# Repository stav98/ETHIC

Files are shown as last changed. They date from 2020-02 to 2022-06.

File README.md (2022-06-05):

# ETHIC
Αποθετήριο με οδηγίες κατασκευής, πηγαίο κώδικα και σχέδια για το έργο " Έξυπνο Θερμοκήπιο Υδροπονικής Καλλιέργειας "<br>
**Ομάδα:** ΚΟΤΣΑΝΙΑ Α.Ε. <br/>
**Σχολείο:** 1ο ΕΠΑ.Λ. Πρέβεζας - Ε.Κ. Πρέβεζας (2019-20, 2020-21)<br/>
**Τίτλος έργου:** Έξυπνο Θερμοκήπιο Υδροπονικής Καλλιέργειας (Ε.Θ.Υ.Κ.)<br/> 

<b>Τελευταία ενημέρωση 5-6-2022</b>

Περιγραφή έργου - Στόχοι
========================
Η ομάδα μας στα πλαίσια του <a href="https://openedtech.ellak.gr/robotics2021/exipno-thermokipio-idroponikis-kalliergias-1o-epa-l-prevezas/">Διαγωνισμού Ανοιχτών Τεχνολογιών στην Εκπαίδευση</a> ο οποίος διοργανώνεται από τον <a href="https://eellak.ellak.gr/">ΕΕΛΛΑΚ</a>, κατασκεύασε <b>μακέτα</b> σύγχρονου θερμοκηπίου υδροπονικής καλλιέργειας το οποίο ελέγχεται εξ' ολοκλήρου από Η/Υ. Το σύστημα εκτός από την δυνατότητα τηλεχειρισμού των λειτουργιών, έχει την δυνατότητα λήψης αποφάσεων ώστε να τηρούνται οι κατάλληλες συνθήκες για την σωστή ανάπτυξη των φυτών. Επιπλέον θα υπάρχει η δυνατότητα αποθήκευσης και γραφικής προβολής όλων των δεδομένων ώστε ο παραγωγός να μπορεί να συσχετίζει την εξέλιξη της παραγωγής σε συνάρτηση με τις συνθήκες του θερμοκηπίου. Έτσι μπορεί να δημιουργήσει μια βάση δεδομένων από την οποία θα αντλεί χρήσιμες πληροφορίες για το κάθε είδος ώστε να μεγιστοποιηθεί η παραγωγή.

Είμαστε μαθητές του τομέα πληροφορικής του 1ου ΕΠΑ.Λ. Πρέβεζας. Η υλοποίηση του έργου έγινε στα εργαστήρια του Ε.Κ. Πρέβεζας μετά την λήξη του διδακτικού ωραρίου.

<table align="center">
 <tr>
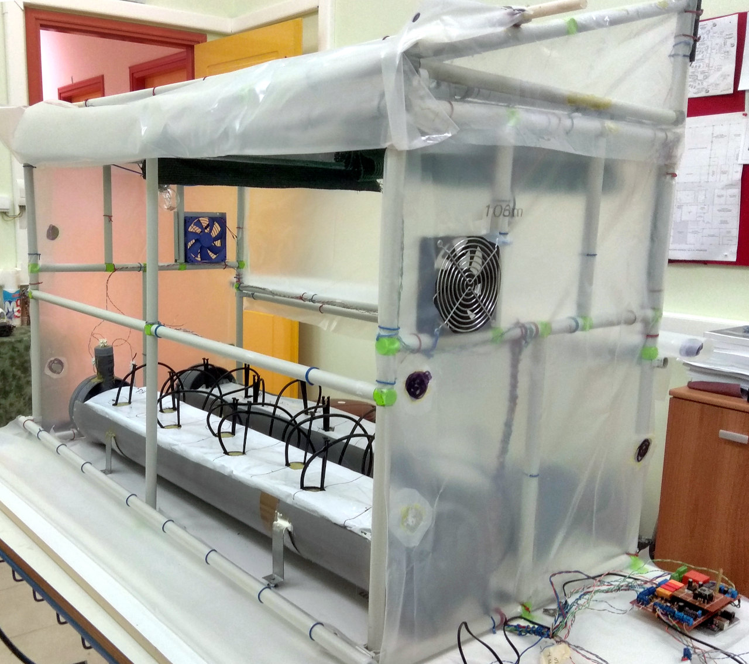
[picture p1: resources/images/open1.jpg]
  <td></td>
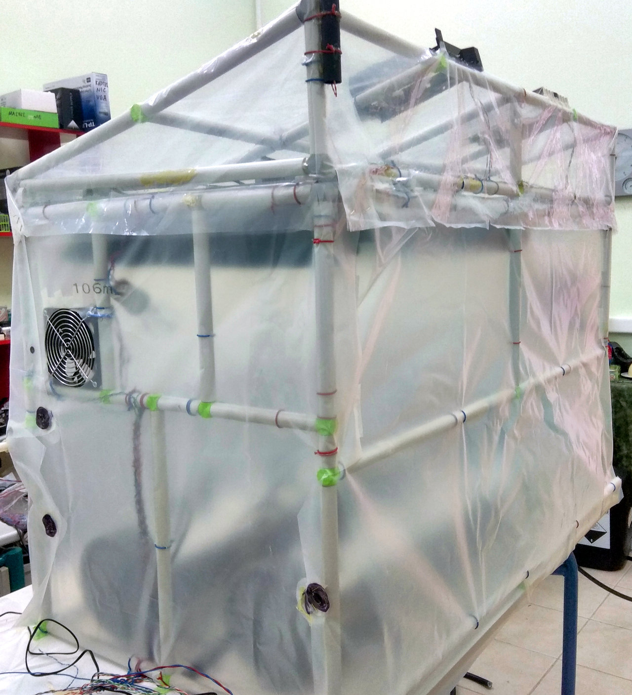
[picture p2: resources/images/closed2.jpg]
  <td></td>
  </tr>
 </table>

Περιεχόμενα
===========

<a href="/md_docs/eisag1.md">Εισαγωγή. Τι είναι η υδροπονία;</a><br>
<a href="/md_docs/eisag2.md">Αρχικός σχεδιασμός του έργου - Στόχοι - Απαιτήσεις και προδιαγραφές.</a><br>
<a href="/md_docs/en6.md">Επίσκεψη σε θερμοκήπιο υδροπονικής καλλιέργειας.</a><br>
<a href="/md_docs/en1.md">Σχεδιασμός μακέτας.</a><br>
<a href="/md_docs/en3.md">Κατασκευή μακέτας.</a><br>
<a href="/md_docs/electrolog.md">Η ηλεκτρολογική εγκατάσταση.</a><br>
Οι συσκευές εξόδου (ενεργοποιητές):<br>
&nbsp;&nbsp;&nbsp;&nbsp;&nbsp;<a href="/md_docs/potisma.md">Το σύστημα ποτίσματος.</a><br>
&nbsp;&nbsp;&nbsp;&nbsp;&nbsp;<a href="/md_docs/skiasi.md">Το σύστημα σκίασης.</a><br>
&nbsp;&nbsp;&nbsp;&nbsp;&nbsp;<a href="/md_docs/eksaerismos.md">Το σύστημα εξαερισμού.</a><br>
&nbsp;&nbsp;&nbsp;&nbsp;&nbsp;<a href="/md_docs/window.md">Τα παράθυρα οροφής.</a><br>
&nbsp;&nbsp;&nbsp;&nbsp;&nbsp;<a href="/md_docs/heating.md">Το σύστημα θέρμανσης.</a><br>
<a href="/md_docs/sensors.md">Οι συσκευές εισόδου (αισθητήρες).</a><br>
<a href="/md_docs/en2.md">Τα ψηφιακά υποσυστήματα ελέγχου και επικοινωνίας.</a><br>
&nbsp;&nbsp;&nbsp;&nbsp;&nbsp;<a href="/md_docs/thermo_node.md">Ο κόμβος ελέγχου των λειτουργιών του θερμοκηπίου.</a><br>
&nbsp;&nbsp;&nbsp;&nbsp;&nbsp;<a href="/md_docs/LoRa_Gateway.md">Η πύλη LoRa Wan Lite.</a><br>
<a href="/md_docs/en4.md">Το πρωτόκολλο LoRa WAN Lite.</a><br>
<a href="https://github.com/stav98/ETHIC/tree/master/NodeRed">Node Red - Η λογική των αυτοματισμών και το γραφικό περιβάλλον.</a><br>

Συμμετέχοντες μαθητές
=====================
<ul>
 <li>Θεοφάνους Ευαγγελία</li>
 <li>Λίτσι Άλντο</li>
 <li>Μιχαηλίδης Γιώργος</li>
 <li>Νέσσερης Θοδωρής</li>
</ul>

Υπεύθυνος καθηγητής: Σταύρος Φώτογλου ΠΕ86 πληροφορικής

Χρονοδιάγραμμα - Στάδια υλοποίησης του έργου
===========================
01/12/19 - 20/12/19 : <a href="md_docs/en1.md">Αρχικός σχεδιασμός ιδέας</a><br/>
08/01/20 - 18/01/20 : <a href="md_docs/en2.md">Σχεδιασμός Hardware</a><br/>
19/01/20 - 29/01/20 : <a href="md_docs/en3.md">Σχεδιασμός 3D εξαρτημάτων και εκτύπωση στον 3D printer</a><br/>
23/01/20 - 30/01/20 : <a href="md_docs/en4.md">Μελέτη πρωτοκόλλου LoRa WAN και κατασκευή του δικού μας απλοποιημένου LoRa WAN Lite</a><br>
01/02/20 - 18/02/20 : Παραγγελία υλικών και ηλεκτρονικών εξαρτημάτων - Έναρξη κατασκευής σκελετού<br>
19/02/20 - 19/02/20 : <a href="md_docs/en6.md">Επίσκεψη σε θερμοκήπιο υδροπονικής καλλιέργειας</a><br/>
20/02/20 - 20/03/20 : Κατασκευή μηχανικών μερών, συστήματος άρδευσης<br/>
............ Διακοπή εργασιών λόγω της πανδημίας ...................<br>
Απρίλιος '21 : Κατασκευή υδραυλικών - αρδευτικών συστημάτων.<br> 
&nbsp;&nbsp;&nbsp;&nbsp;&nbsp;&nbsp;&nbsp;&nbsp;&nbsp;-//-&nbsp;&nbsp;&nbsp;&nbsp;&nbsp;&nbsp;&nbsp;&nbsp;: Δοκιμές άρδευσης.<br>
&nbsp;&nbsp;&nbsp;&nbsp;&nbsp;&nbsp;&nbsp;&nbsp;&nbsp;-//-&nbsp;&nbsp;&nbsp;&nbsp;&nbsp;&nbsp;&nbsp;&nbsp;: Κατασκευή συστήματος σκίασης - Δοκιμές.<br>
Μάϊος '21    : Πέρασμα καλωδίωσης - ηλεκτρολογική εγκατάσταση.<br>
&nbsp;&nbsp;&nbsp;&nbsp;&nbsp;&nbsp;&nbsp;&nbsp;&nbsp;-//-&nbsp;&nbsp;&nbsp;&nbsp;&nbsp;&nbsp;&nbsp;&nbsp;: Τοποθέτηση συστημάτων ποτίσματος - δοκιμές.<br>
&nbsp;&nbsp;&nbsp;&nbsp;&nbsp;&nbsp;&nbsp;&nbsp;&nbsp;-//-&nbsp;&nbsp;&nbsp;&nbsp;&nbsp;&nbsp;&nbsp;&nbsp;: Τοποθέτηση νάυλον.<br>
Ιούνιος '21  : Διόρθωση αρχικών σχεδίων.<br>
&nbsp;&nbsp;&nbsp;&nbsp;&nbsp;&nbsp;&nbsp;&nbsp;&nbsp;-//-&nbsp;&nbsp;&nbsp;&nbsp;&nbsp;&nbsp;&nbsp;&nbsp;&nbsp;: <a href="md_docs/en15.md">Κατασκευή πρωτότυπου ηλεκτρονικού κυκλώματος σε perfboard.</a><br>
&nbsp;&nbsp;&nbsp;&nbsp;&nbsp;&nbsp;&nbsp;&nbsp;&nbsp;-//-&nbsp;&nbsp;&nbsp;&nbsp;&nbsp;&nbsp;&nbsp;&nbsp;&nbsp;: Δοκιμές του πρωτοκόλλου LoRa WAN Lite. <br>
Σεπτέμβριος '21  : Συγγραφή τεκμηρίωσης - σύνδεση υποσυστημάτων - δοκιμές.<br>
<br>
Το έργο θα βελτιώνεται και αναβαθμίζεται συνεχώς από μαθητές επόμενων τάξεων. <b>Τελευταία ενημέρωση: Μαϊος 2022</b>
<br>
<table align="center">
 <tr>
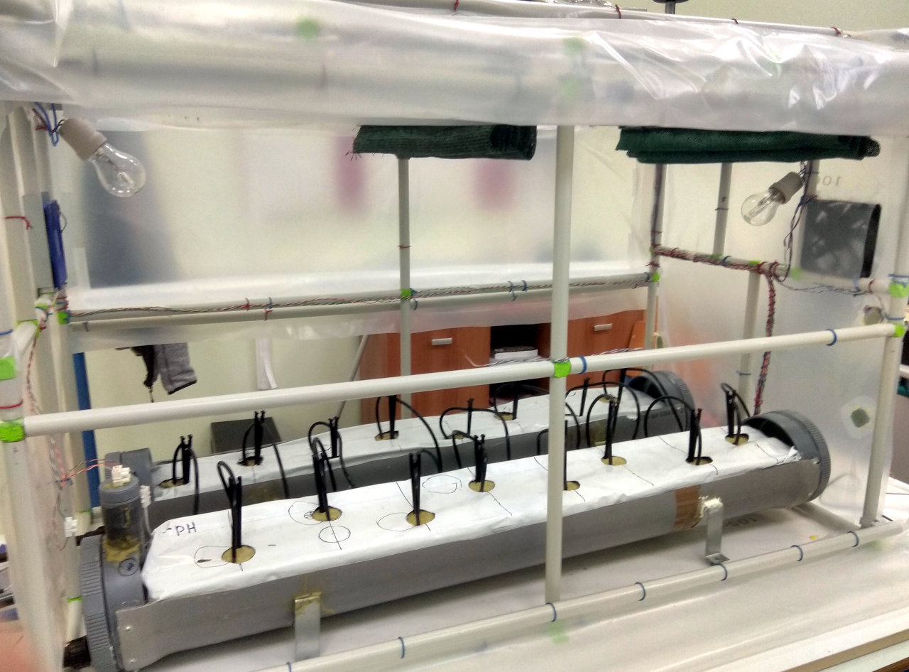
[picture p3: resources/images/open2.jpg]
  <td></td>
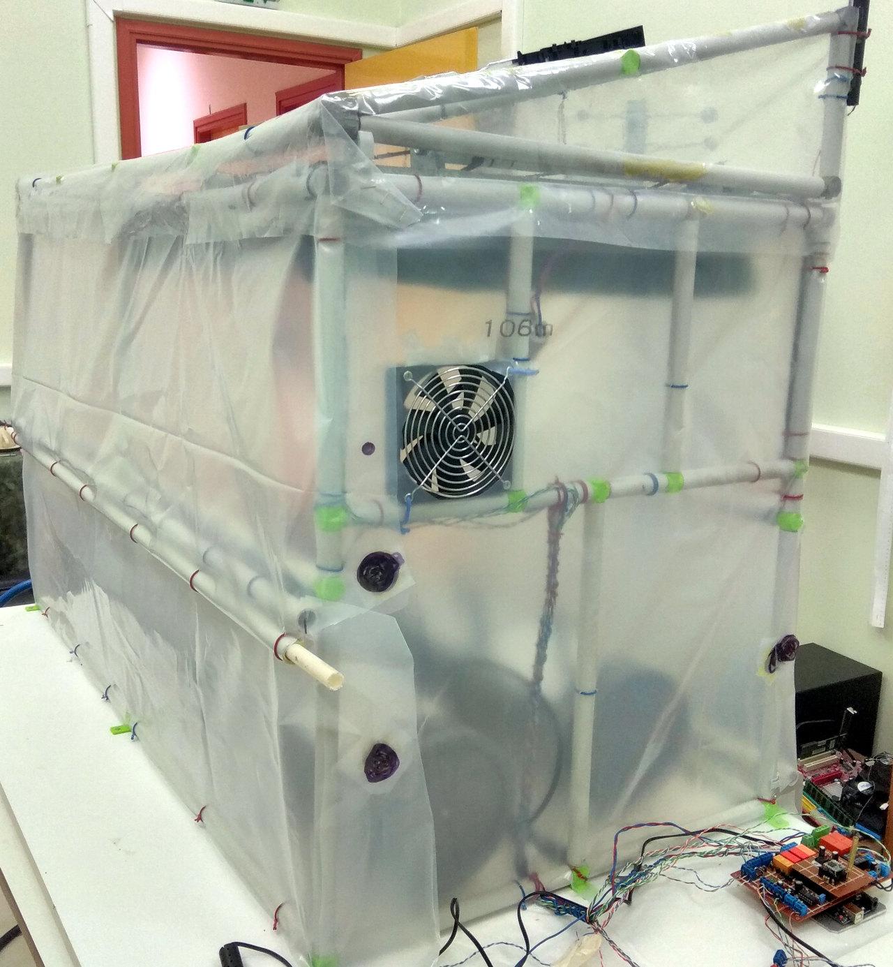
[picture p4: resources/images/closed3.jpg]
  <td></td>
 </tr>
 <tr>
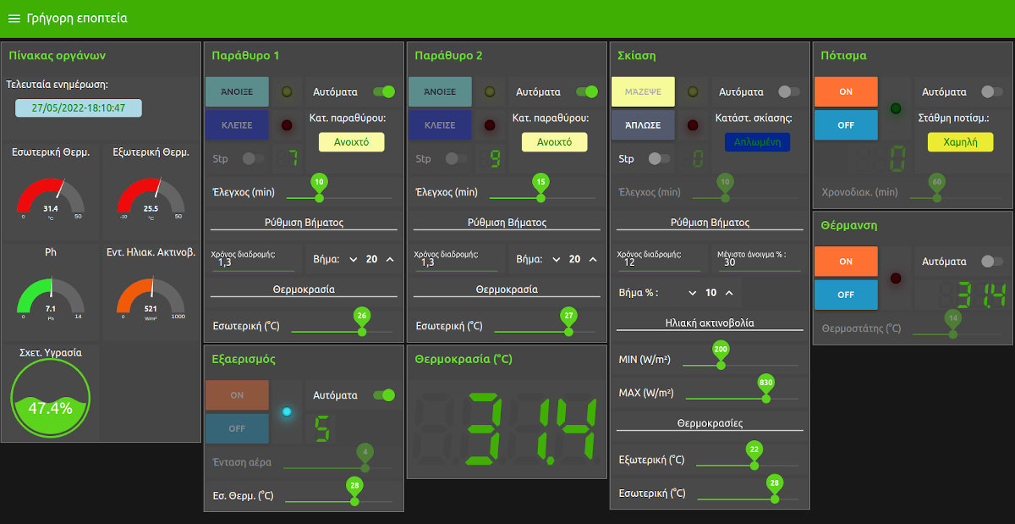
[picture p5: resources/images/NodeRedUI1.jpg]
  <td></td>
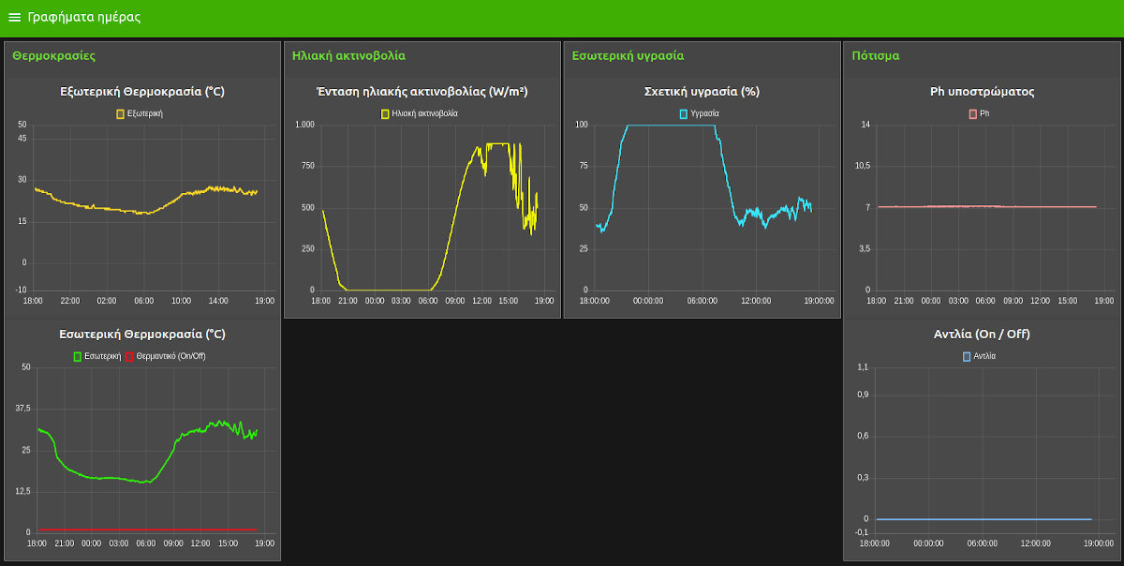
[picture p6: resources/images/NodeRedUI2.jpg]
  <td></td>
 </tr>
 </table>

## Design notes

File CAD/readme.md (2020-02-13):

Στον κατάλογο αυτό υπάρχουν τα σχέδια της κατασκευής καθώς και των εξαρτημάτων τα οποία εκτυπώνονται στον 3D printer.

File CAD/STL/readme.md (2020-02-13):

Εδώ υπάρχουν τα αρχεία των εξαρτημάτων και του μοντέλου σε μορφή .stl, για εκτύπωση στον 3D printer.

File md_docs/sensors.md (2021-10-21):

<a href="../README.md"><= Επιστροφή</a><br>

<p>Παρακάτω φαίνονται οι αισθητήρες του θερμοκηπίου. Για την εξωτερική θερμοκρασία χρησιμοποιήσαμε ένα θερμόμετρο OneWire με ακρίβεια 0,5°C. Για την εσωτερική θερμοκρασία και υγρασία βάλαμε το DHT22. Για την ένταση της ηλιακής ακτινοβολίας Irradiation βάλαμε ένα φτηνό φωτοβολταϊκό από φώτα κήπου. Αυτό σε φορτίο 100Ω παράγει τάση 2V περίπου. Για την πλήρωση της στάθμης ποτίσματος βάλαμε δύο μεταλλικά probe τα οποία μόλις έρθουν και τα δύο σε επαφή με νερό ενημερώνουν τον μικροελεγκτή. Τέλος για μετρητή pH βάλαμε ένα probe από ένα φτηνό όργανο γλάστρας αξίας περίπου 10€. Αυτό έχει μικρή ακρίβεια και μετράει τιμές από 2 (όξινο) έως 12 (αλκαλικό ή βασικό), αλλά για τον σκοπό του έργου μας είναι αρκετό. Το probe του Ph καρφώνεται οριζόντια στο υπόστρωμα του πετροβάμβακα ώστε να μετράει συνέχεια το Ph που υπάρχει στις ρίζες του φυτού. Κάθε καλλιέργεια χρειάζεται τροφή με διαφορετικό Ph ώστε να έχουμε την μέγιστη απόδοση.</p>
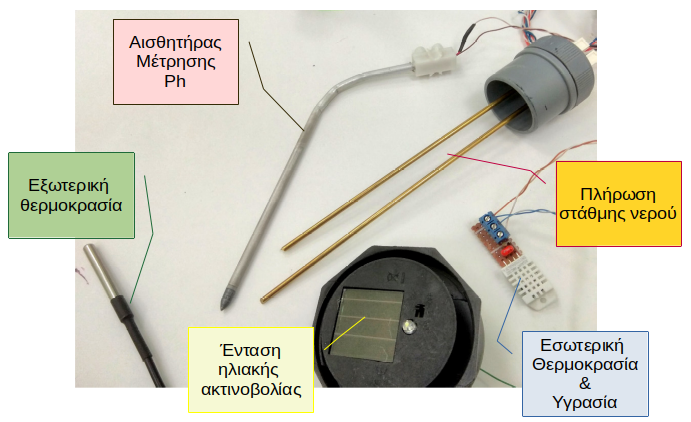
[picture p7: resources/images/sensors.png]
  
  <p>Στην επόμενη εικόνα φαίνονται οι αισθητήρες πλήρωσης και Ph και ο τρόπος που τοποθετούνται. </p>
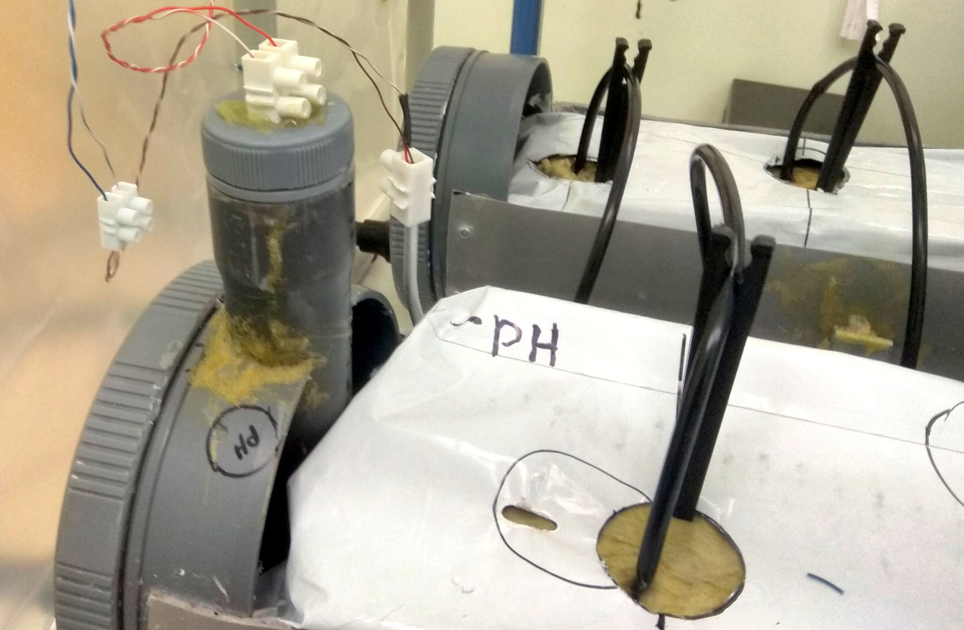
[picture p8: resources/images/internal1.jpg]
  

  <a href="../README.md"><= Επιστροφή</a><br>

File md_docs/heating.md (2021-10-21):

<a href="../README.md"><= Επιστροφή</a><br>

<p>Για θέρμανση χρησιμοποιήσαμε δύο λάμπες πυρακτώσεως των 100W η κάθε μία. Προσοχή οι λάμπες λειτουργούν με 220V. Όταν η εξωτερική θερμοκρασία είναι κάτω από 5°C και η εσωτερική έχει κατέβει κάτω από την ελάχιστη θερμοκρασία ανοχής της καλλιέργειας τότε αυτόματα το Arduino δίνει εντολή και ανάβει τις λάμπες. Φυσικά τα παράθυρα της οροφής είναι κλειστά. Επιπλέον αν δεν υπάρχει ηλιοφάνεια, το σύστημα απλώνει τις κουρτίνες ώστε να μειωθεί ο όγκος του χώρου και να μη χάνουμε θερμότητα από την οροφή.</p>
  

  <a href="../README.md"><= Επιστροφή</a><br>

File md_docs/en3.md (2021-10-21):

<a href="../README.md"><= Επιστροφή</a><br>

<p>Αρχικά σχεδιάσαμε στο λογισμικό ανοιχτού κώδικα FreeCad την μακέτα και εκτυπώσαμε τον σκελετό σε κλίμακα 1:10, ώστε να έχουμε μια εικόνα πριν την έναρξη της κατασκευής. Όλα τα αρχεία για την κατασκευή των εξαρτημάτων <a href="../CAD">βρίσκονται εδώ</a>.</p>
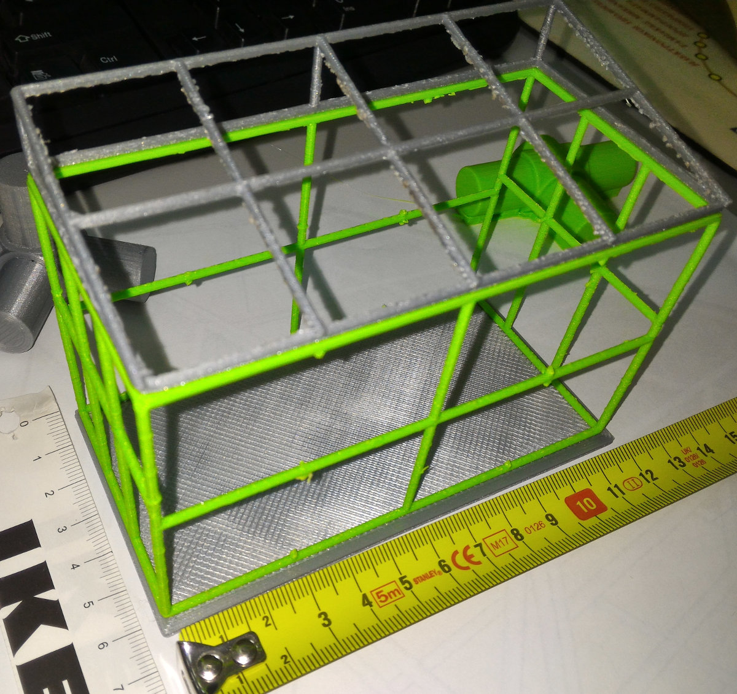
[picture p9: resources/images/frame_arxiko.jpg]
  
<p>Μετά σχεδιάσαμε τα εξαρτήματα των συνδέσμων στο FreeCad και τα εκτυπώσαμε στον εκτυπωτή 3D του σχολείου μας.</p>
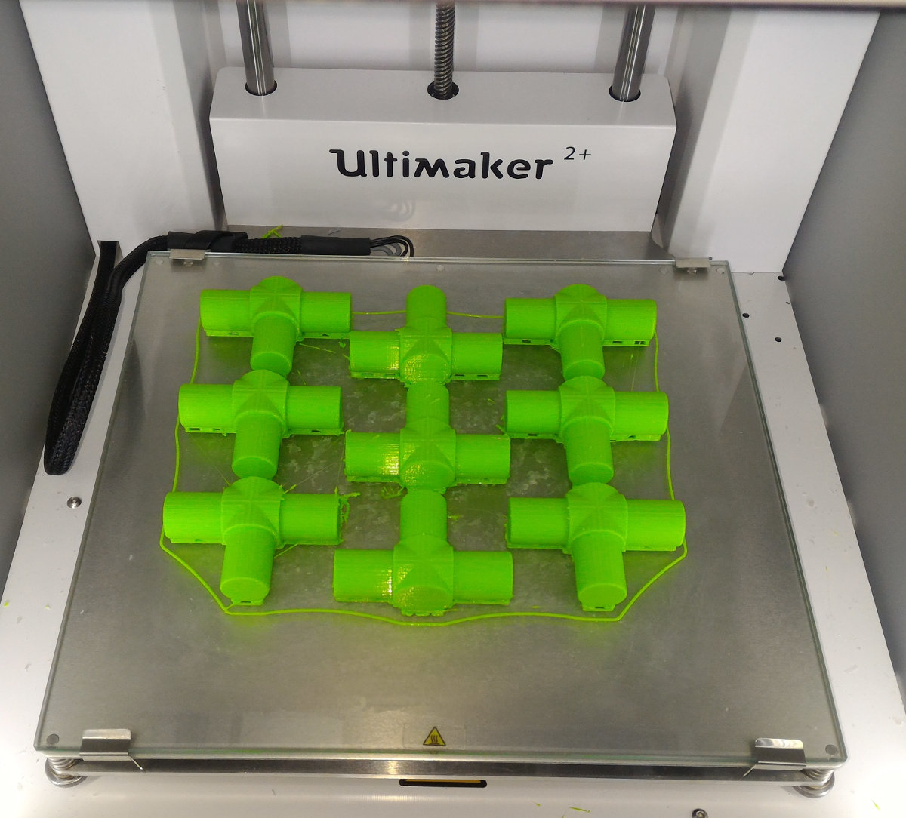
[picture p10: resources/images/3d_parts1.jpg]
  
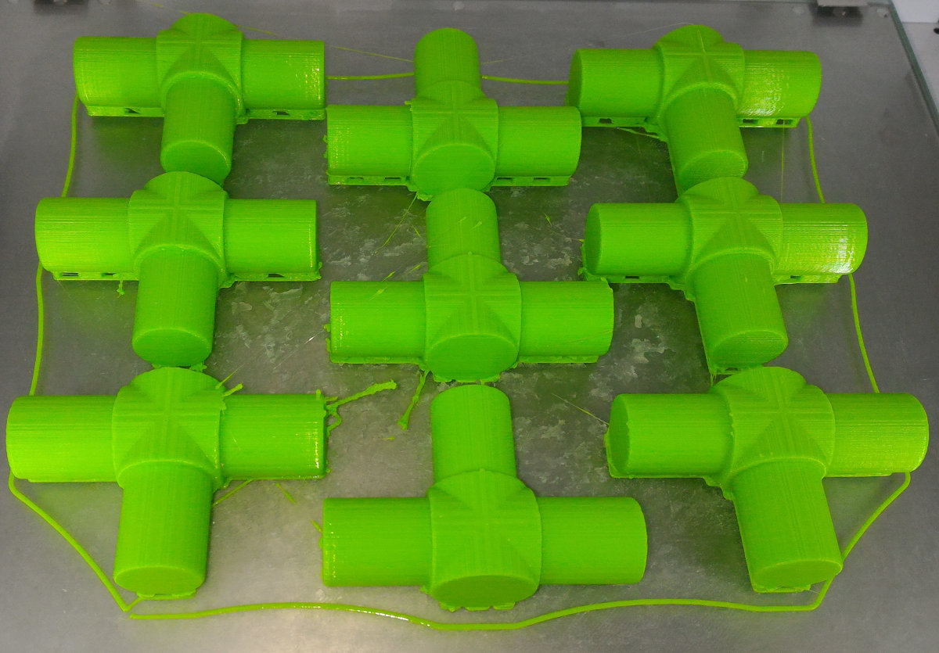
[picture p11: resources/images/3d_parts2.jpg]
  
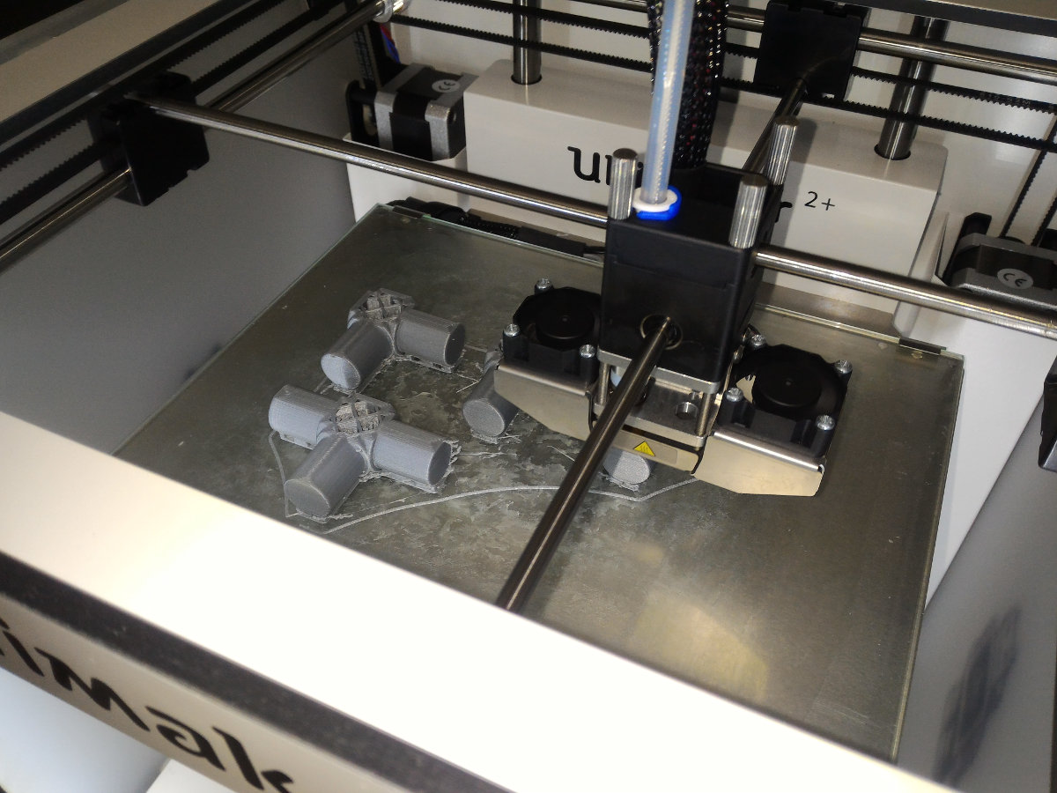
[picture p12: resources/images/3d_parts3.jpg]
  
<p>Ακολουθεί video:</p>
  <p align="center">

</p>
<p>Και μετά συναρμολογήσαμε τον σκελετό της μακέτας. Χρησιμοποιώντας εργαλεία χειρός όπως λίμες, πριόνι και γυαλόχαρτο, εξομαλύναμε τα εξαρτήματα και μετά ενώσαμε τους σωλήνες PVC βάσει του αρχικού σχεδίου.<p>
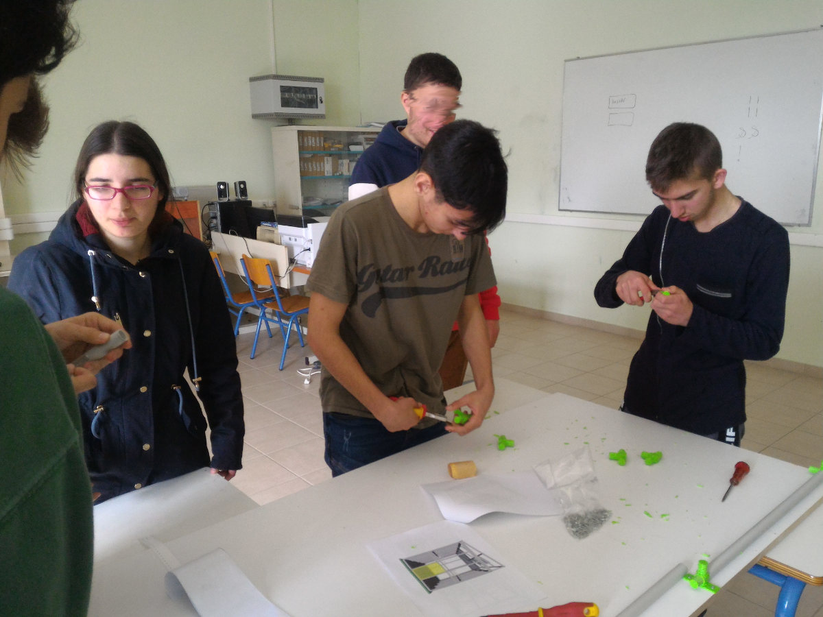
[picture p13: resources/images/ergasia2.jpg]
  
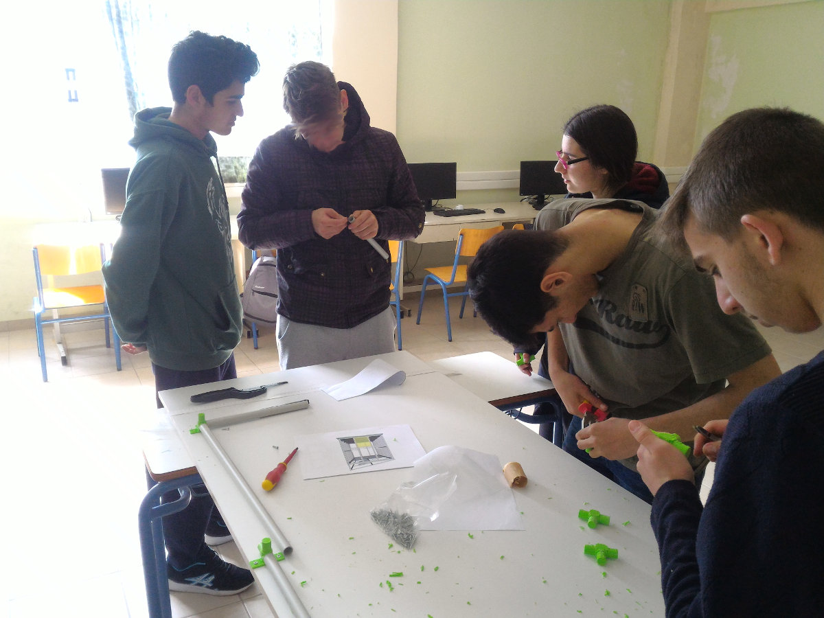
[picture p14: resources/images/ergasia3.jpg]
  
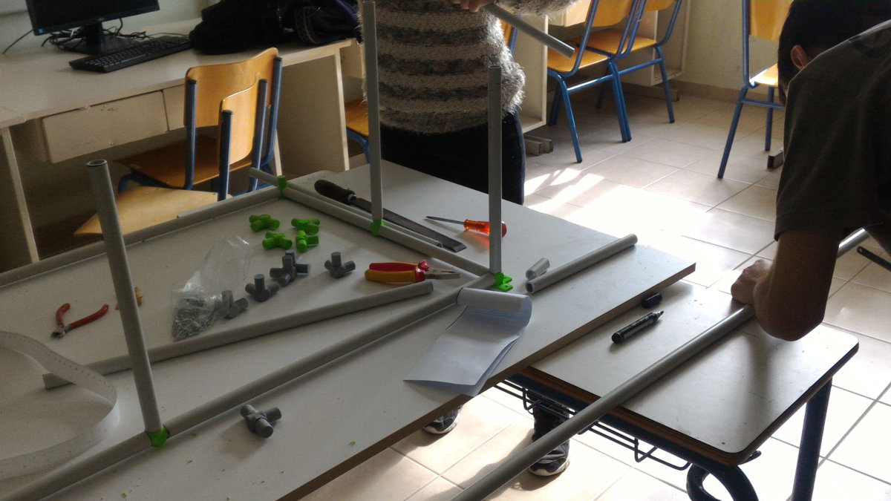
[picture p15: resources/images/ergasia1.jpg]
  
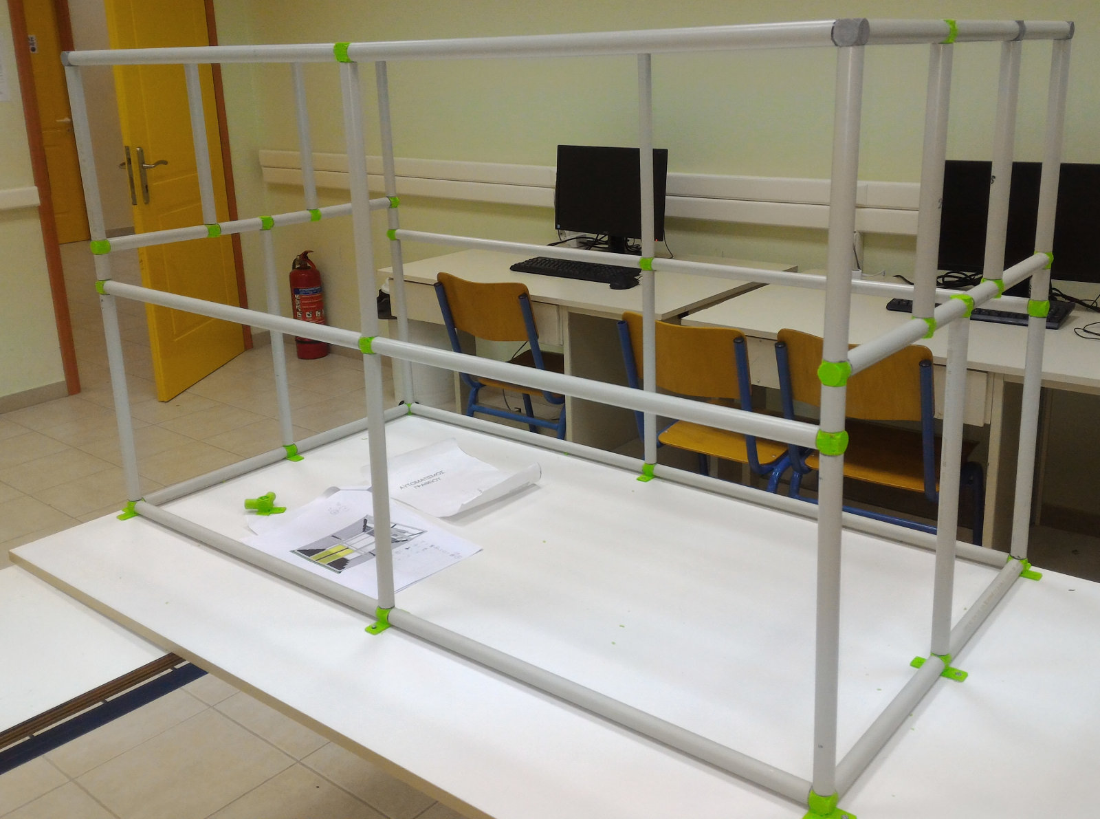
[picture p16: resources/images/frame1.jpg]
  
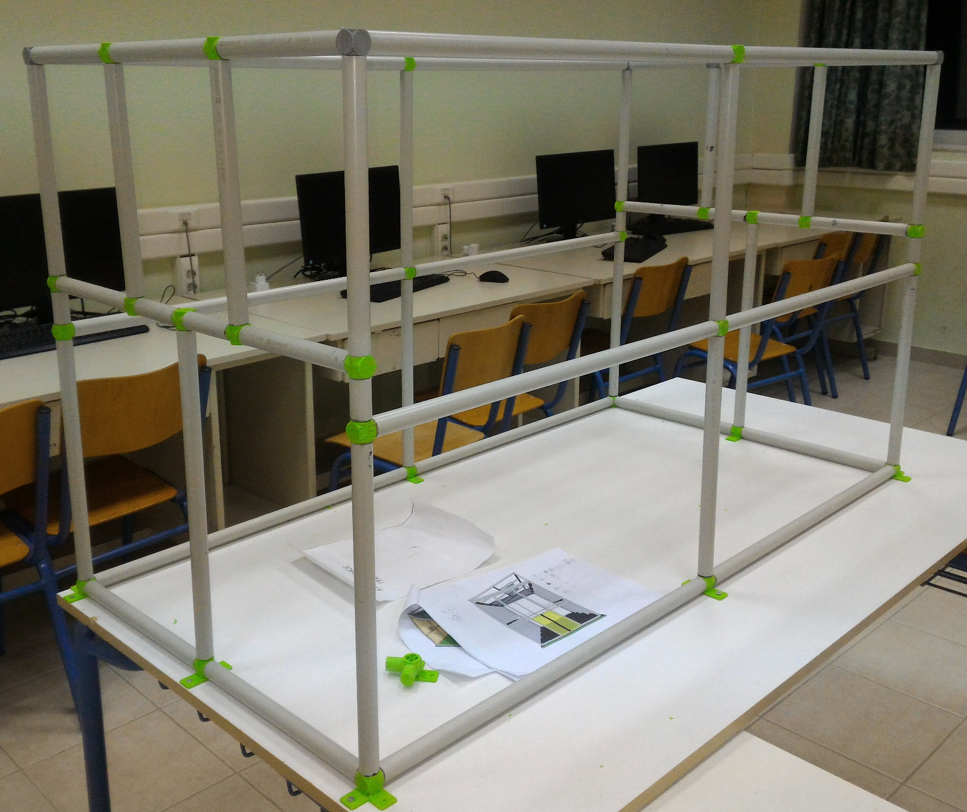
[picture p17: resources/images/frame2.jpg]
  
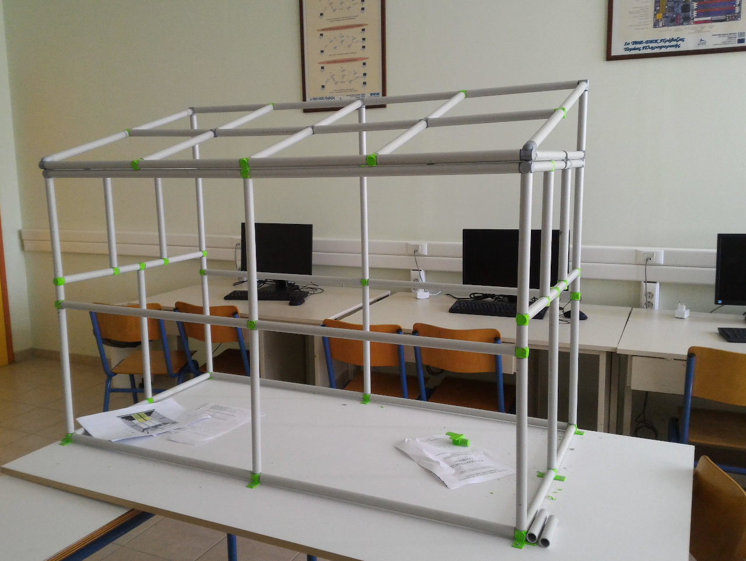
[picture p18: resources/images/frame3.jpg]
  
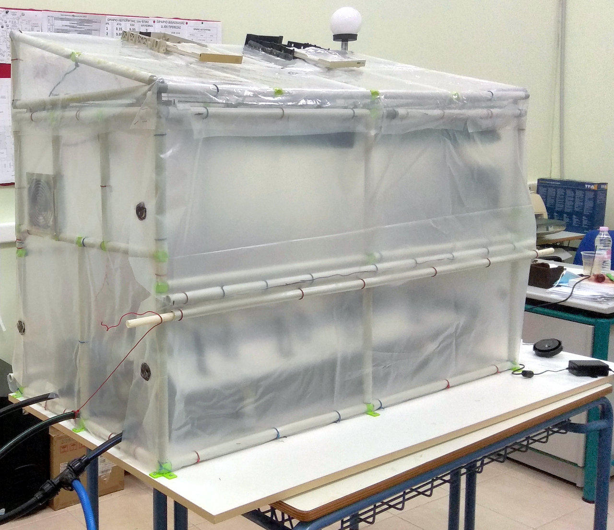
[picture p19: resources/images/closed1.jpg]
  
  
<p>Ακολουθεί video:</p>
  <p align="center">

</p>
  <a href="../README.md"><= Επιστροφή</a><br>

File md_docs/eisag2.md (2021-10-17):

<a href="../README.md"><= Επιστροφή</a><br>
  
Αρχικός Σχεδιασμός
==================

Θα κατασκευάσουμε μια μακέτα θερμοκηπίου από νάυλον διαστάσεων περίπου 120cm x 60cm x95cm. Μέσα θα τοποθετηθούν όλα τα εξαρτήματα και οι συσκευές που χρησιμοποιούνται σε ένα πραγματικό θερμοκήπιο. Συγκεκριμένα θα βάλουμε τα εξής:  
1.	Στοιχεία θέρμανσης του αέρα
2.	Αυτόματο πότισμα
3.  Εξαερισμό με ανεμιστήρες
4.  Σύστημα αυτόματης σκίασης
5.  Σύστημα ελέγχου των παραθύρων

Ένα πλήθος αισθητήρων θα τροφοδοτεί με δεδομένα τον κεντρικό Η/Υ ώστε να λαμβάνονται οι αποφάσεις για τον έλεγχο των παραπάνω συσκευών. Θα τοποθετήσουμε αισθητήρες:
1.  Θερμοκρασίας
2.  Ηλιοφάνειας
3.  PH
4.  Ποτίσματος
5.  Υγρασίας αέρα

Μέσα στο σπογγώδες υπόστρωμα θα φυτέψουμε φυτά ώστε να κάνουμε τις δοκιμές μας σε πραγματικές συνθήκες.

Επειδή το θερμοκήπιο μπορεί να είναι απομακρυσμένο και να μην υπάρχει δυνατότητα σύνδεσης με το διαδίκτυο (εκτός από δίκτυα 3G-4G-5G τα οποία έχουν και το ανάλογο κόστος χρήσης), θα χρησιμοποιήσουμε το σύστημα μετάδοσης LO.RA. για την επικοινωνία με τον 2ο χώρο π.χ. το σπίτι του παραγωγού, όπου θα υπάρχει σύνδεση με το διαδίκτυο. Το σύστημα LO.RA. μπορεί να καλύψει μεγάλες αποστάσεις (έως 30Km) για χαμηλούς ρυθμούς μετάδοσης. Επειδή το θερμοκήπιό μας δεν στέλνει και πολλά δεδομένα από τους αισθητήρες του, το πρωτόκολλο LORA WAN είναι ιδανικό. Σήμερα λειτουργούν αρκετά δίκτυα LORA WAN σε όλο τον κόσμο και χρησιμοποιούνται σε συστήματα IOT όταν είναι απομακρυσμένα και θέλουμε χαμηλή κατανάλωση ενέργειας.  

<p align = "center">
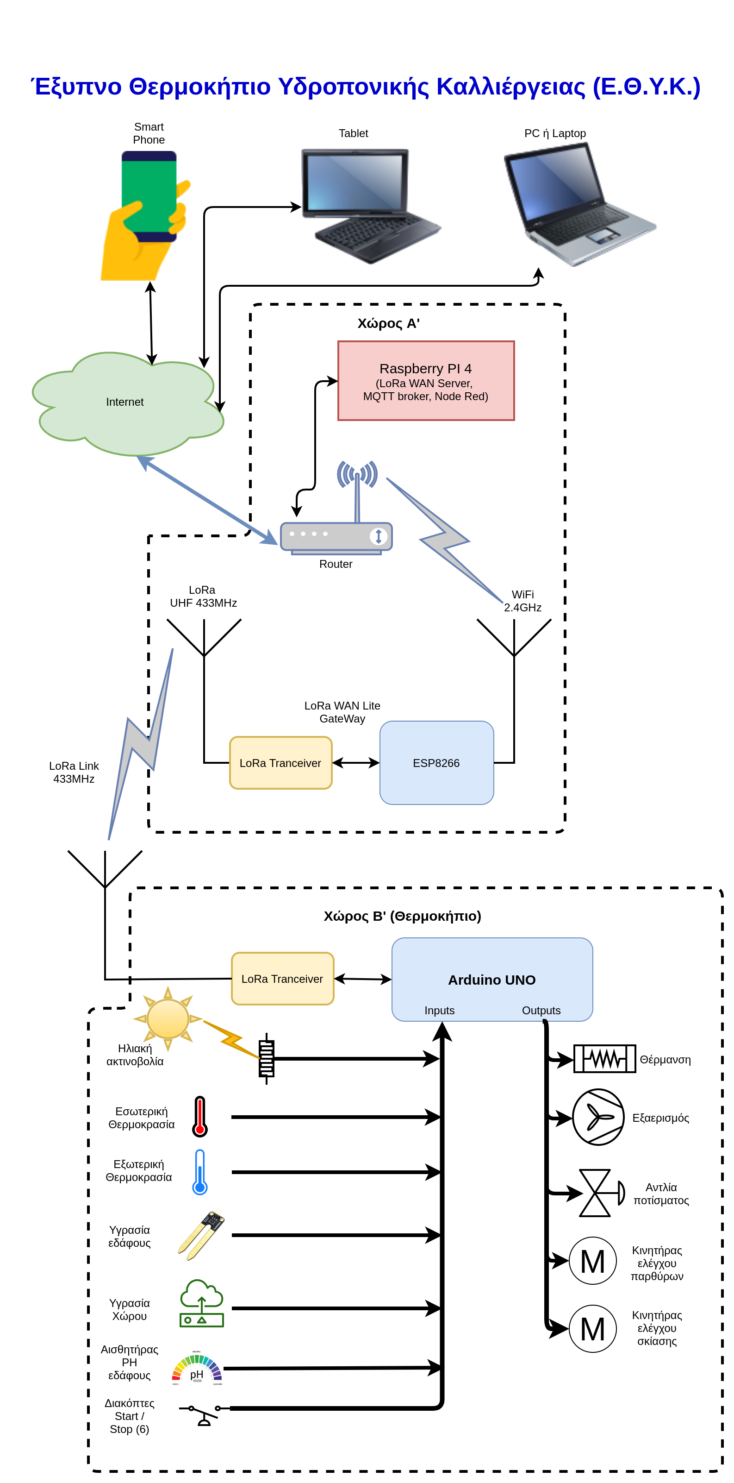
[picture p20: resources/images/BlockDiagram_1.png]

</p>

Όπως φαίνεται στο σχήμα στο θερμοκήπιο (Χώρος Β') υπάρχουν όλοι οι αισθητήρες και οι ενεργοποιητές οι οποίοι συνδέονται σ' ένα arduino. Επίσης στο arduino συνδέεται ένα άρθρωμα LORA το οποίο στέλνει τα δεδομένα και δέχεται εντολές από τον κεντρικό υπολογιστή ο οποίος βρίσκεται στον χώρο Α'. Ο κώδικας στο arduino θα γραφτεί σε Wiring. Τα δεδομένα είναι κωδικοποιημένα και κρυπτογραφημένα σύμφωνα με το πρωτόκολλο LORA WAN. 

Από την άλλη πλευρά (Χώρος Α΄), υπάρχει μια απλή πύλη LORA WAN η οποία στέλνει τα δεδομένα στο διαδίκτυο με το πρωτόκολλο MQTT. Στη πύλη μπορούν να συνδεθούν περισσότερα θερμοκήπια και να διαχειρίζονται από το ίδιο ή διαφορετικούς servers. Το λογισμικό της πύλης ενώ αρχικά το γράψαμε σε micropython, παρουσιάστηκαν προβλήματα καθυστέρησης και εδώ οι χρόνοι είναι κρίσιμοι. Έτσι το μεταφέραμε και αυτό σε wiring. 

Τέλος ο εξυπηρετητής μπορεί να είναι οποιοσδήποτε υπολογιστής με Linux, στον οποίο θα τρέχει το mosquitto (MQTT Broker) και το Node Red. Εδώ μπορούμε να προσθέσουμε και μερικά δικά μας script σε Python τα οποία θα ακούν ή θα δημοσιεύουν σε mqtt topics. Εμείς για εξυπηρετητή σκοπεύουμε να χρησιμοποιήσουμε ένα Raspberry PI 3 ή 4.

Τελική υλοποίηση
================
  
Το υλικό ελέγχου έχει χωριστεί σε τρία μέρη:

1. Κεντρικός διακομιστής
Ο διακομιστής μας θα είναι ένα Raspberry PI 4 στο οποίο θα εγκατασταθούν τα πακέτα: Mosquitto MQTT broker, Node Red και Network Server το οποίο γράψαμε σε Python 3. Το Raspberry μπορεί να βρίσκεται οπουδήποτε αρκεί να υπάρχει σύνδεση με το διαδίκτυο, να έχουν ανοίξει οι συγκεκριμένες πόρτες του router και να κατευθύνονται στο Raspberry. Επίσης αν έχουμε δυναμική απόδοση διεύθυνσης IP, πρέπει να φαίνεται στον έξω κόσμο μέσω κάποιου παρόχου δυναμικού DNS π.χ. FreeDNS, DynDNS κλπ. Εναλλακτικά μπορούμε να βάλουμε ένα PC με Linux ή να νοικιάσουμε κάποιο VPS με Linux.

2. Πύλη επικοινωνίας LoRa Wan Lite
Η πύλη LoRa είναι μια διαφανής πύλη η οποία λαμβάνει πλαίσια LoRa WAN από τους ελεγκτές θερμοκηπίων - κόμβους και τα προωθεί στο διαδίκτυο και συγκεκριμένα στο Raspberry Pi 4 ή τον διακομιστή τον οποίο στήσαμε στην προηγούμενη παράγραφο. Επίσης παίρνει πακέτα από τον διακομιστή και τα προωθεί στους ελεγκτές - κόμβους. Η πύλη τοποθετείται οπουδήποτε αρκεί να έχει πρόσβαση στο διαδίκτυο. Επειδή τα θερμοκήπια μπορεί να είναι αρκετά μακριά, η πύλη μπορεί να εγκατασταθεί στο σπίτι του παραγωγού.

3. Ελεγκτής θερμοκηπίου - Κόμβος
Οι κόμβοι μπορούν να βρίσκονται σε διαφορετικά μέρη και σε απόσταση μέχρι 20Km από την πύλη αρκεί να μην υπάρχουν πολλά φυσικά εμπόδια όπως κτίρια ή βουνά.

Το έργο μπορεί να χρησιμοποιηθεί ως εποπτικό μέσο για την διδασκαλία των τεχνολογιών IOT σε μαθητές των τομέων Πληροφορικής, Ηλεκτρονικής - Ηλεκτρολογίας καθώς και για την μελέτη σύγχρονων καλλιεργητικών μεθόδων από μαθητές του τομέα Γεωπονίας και Τροφίμων.
<br><br>
<a href="../README.md"><= Επιστροφή</a><br>

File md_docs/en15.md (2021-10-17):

<a href="../README.md"><= Επιστροφή</a><br>

<p>Η κατασκευή του κόμβου και της πύλης LoRa Wan Lite έγιναν σε perfboard. Στην παρακάτω φωτογραφία φαίνεται η συνδεσμολογία των αισθητήρων και ενεργοποιητών του θερμοκηπίου.</p>
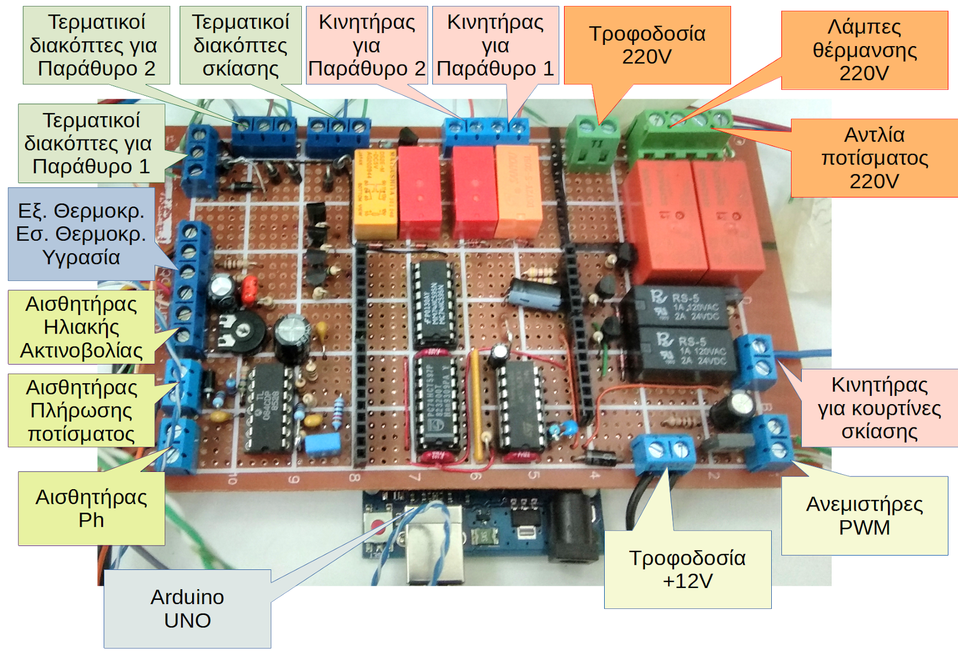
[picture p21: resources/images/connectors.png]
  
  
  <a href="../README.md"><= Επιστροφή</a><br>

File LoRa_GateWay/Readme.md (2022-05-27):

<p>Η πύλη LoRa Wan Lite δέχεται πακέτα από τους κόμβους δηλαδή τα θερμοκήπια και τα προωθεί στον Network Server. Η επικοινωνία είναι αμφίδρομη γιατί η πύλη δέχεται πακέτα από τον Network Server και τα στέλνει στου κόμβους ώστε να κάνουν κάποια ενέργεια π.χ. πότισμα, εξαερισμό κλπ.</p>
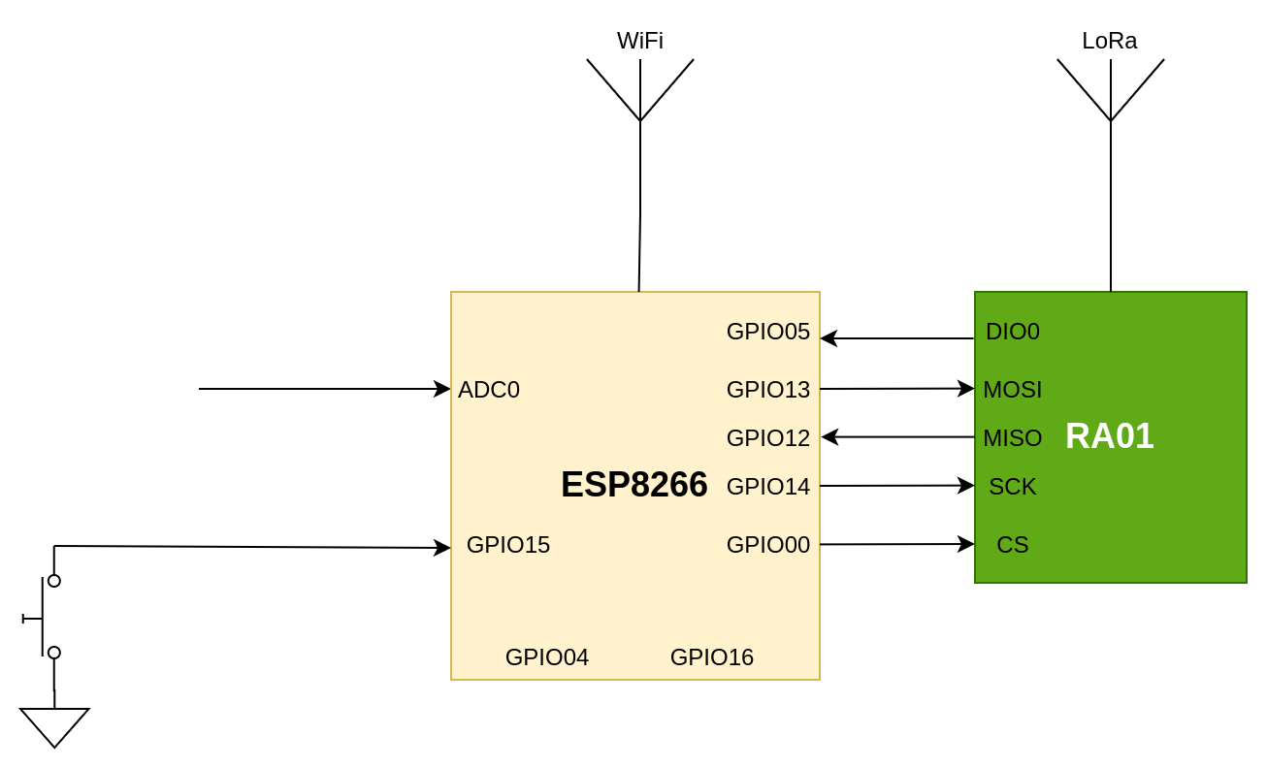
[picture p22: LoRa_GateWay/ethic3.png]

<p>Όλες οι ρυθμίσεις της πύλης γίνονται μέσω Web Interface. Επίσης στην αρχική οθόνη βλέπουμε την κατάσταση της πύλης καθώς και τα τελευταία LoRa Wan Lite frames που έλαβε και έστειλε.</p>
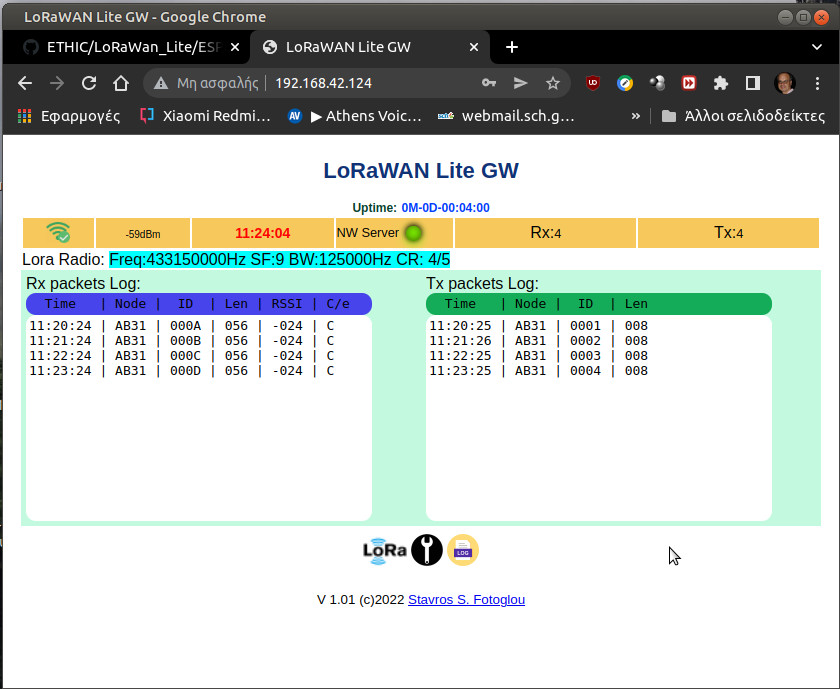
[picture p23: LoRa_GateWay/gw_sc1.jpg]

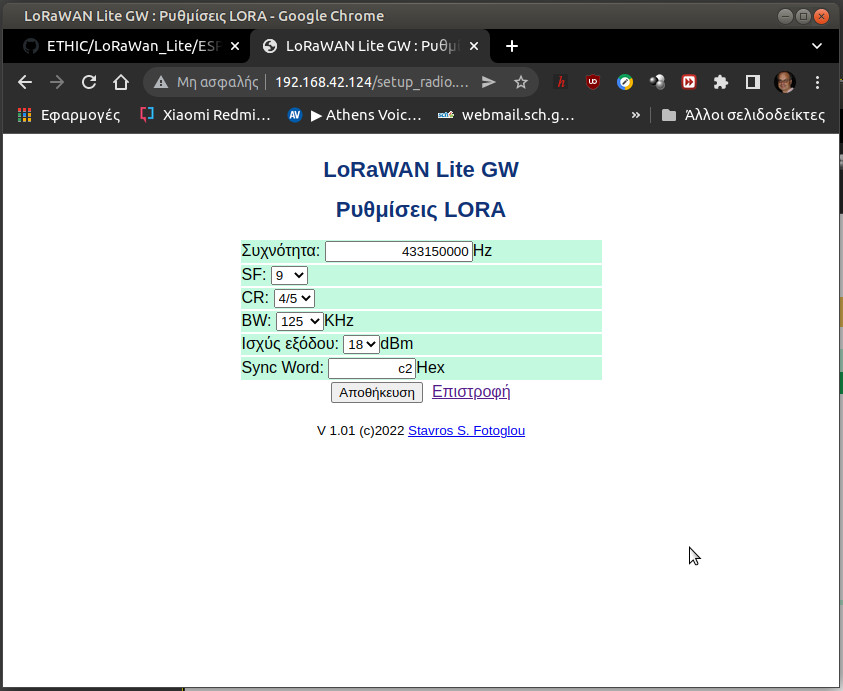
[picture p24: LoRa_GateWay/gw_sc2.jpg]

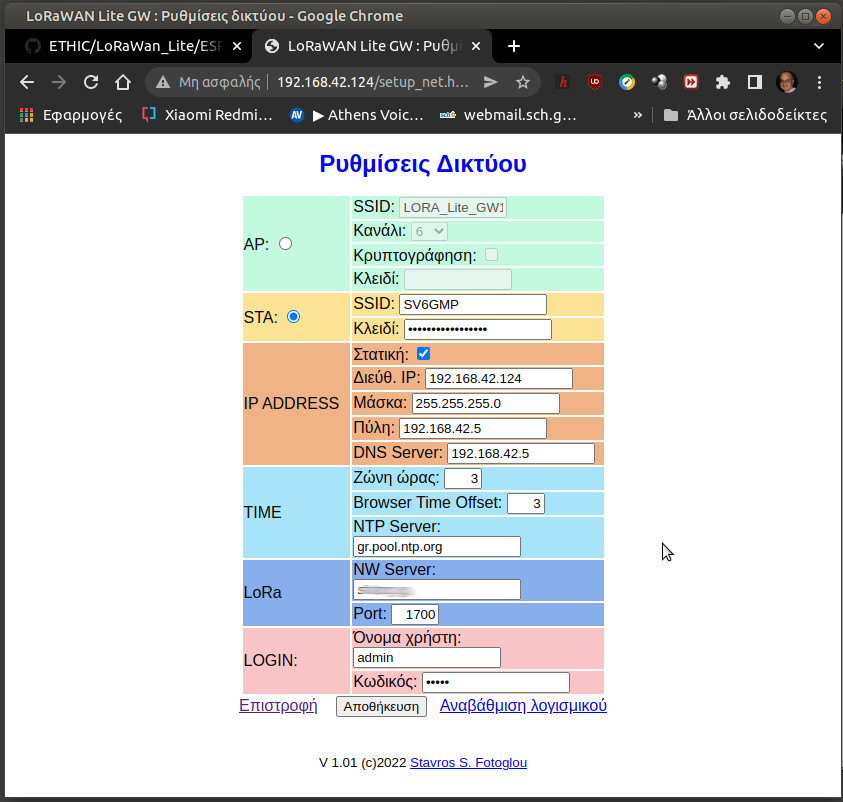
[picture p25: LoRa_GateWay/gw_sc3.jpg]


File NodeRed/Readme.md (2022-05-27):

<a href="../README.md"><= Επιστροφή</a><br>
<p>Στο Raspberry PI 3 ή 4 εγκαθιστούμε το Node Red. Εναλλακτικά μπορεί να εγκατασταθεί και σε κάποιον απομακρυσμένο server. Το Node Red δημοσιεύει και δέχεται μηνύματα από τον τοπικό ή απομακρυσμένο mqtt broker και εμφανίζει με όμορφο γραφικό τρόπο τα αποτελέσματα. Επίσης μπορούμε να στείλουμε εντολές στο θερμοκήπιο μέσα από το γραφικό περιβάλλον. Επειδή ο απομακρυσμένος κόμβος στο θερμοκήπιο, λειτουργεί σε τάξη Α' (δηλ. εκπέμπει σε τακτά χρονικά διαστήματα και ανοίγει δύο παράθυρα λήψης 1 και 2 sec μετά), αν εμείς δώσουμε μια εντολή, αυτή θα εκτελεστεί μετά από 1 λεπτό το πολύ. Για να έχουμε κύκλο χρήσης (duty cycle) κάτω από 1% όπως προβλέπεται από τους κανονισμούς ραδιοεπικοινωνιών στη χώρα μας, βάλαμε χρόνο εκπομπής του κόμβου κάθε 1 λεπτό.</p>
<p>Εδώ πρέπει να επισημάνουμε ότι τα τρία προγράμματα τα οποία τρέχουν τοπικά στο Raspberry PI, δηλ. ο Network Server ο οποίος δέχεται και στέλνει πακέτα LoRa Wan Lite στην πύλη, o MQTT broker mosquitto ο οποίος δέχεται και στέλνει μηνύματα στα Nodes μέσα από τον Network Server και την πύλη και το Node Red το οποίο υλοποιεί την λογική λειτουργίας και το γραφικό περιβάλλον, μπορούν να βρίσκονται σε ξεχωριστούς server στο διαδίκτυο.</p>


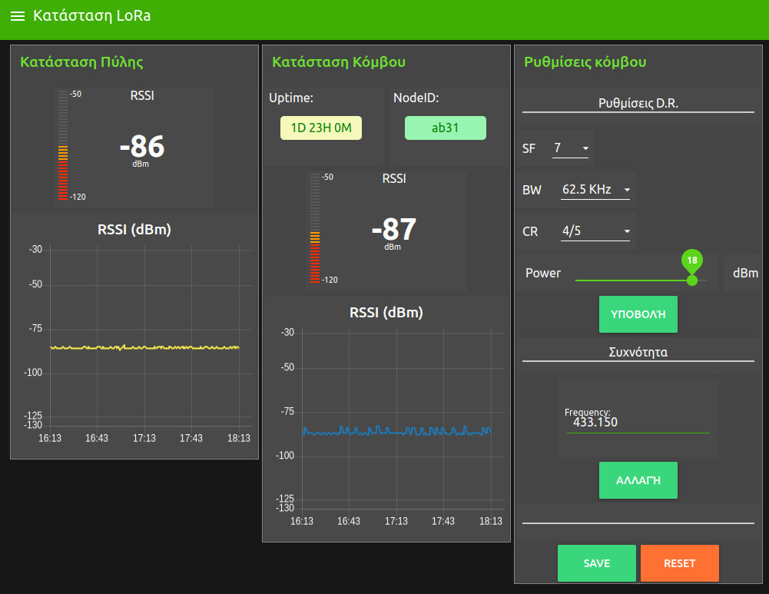
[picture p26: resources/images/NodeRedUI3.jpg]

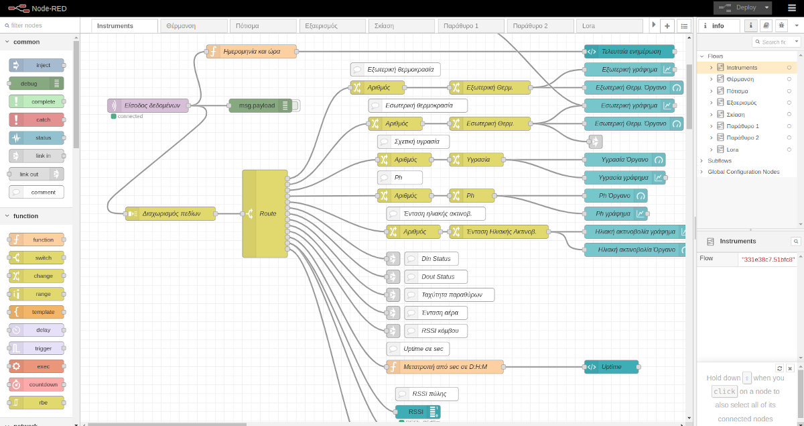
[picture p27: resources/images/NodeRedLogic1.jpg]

<a href="../README.md"><= Επιστροφή</a><br>

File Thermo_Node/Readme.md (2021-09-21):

Εδώ υπάρχει το Υλικό (Block διαγράμματα και ηλεκρονικά - ηλεκτρολογικά σχέδια) και Λογισμικό για τα υποσυστήματα μέσα στο θεμοκήπιο.
Μέσα σε κάθε θερμοκήπιο υπάρχει ένας κόμβος ο οποίος επικοινωνεί μέσω LoRa με την πύλη LoRa Wan. Ο κόμβος κάνει μετρήσεις μέσω των αισθητήρων σε τακτά χρονικά διαστήματα π.χ. 60 sec και τις στέλνει στην πύλη. Η πύλη στέλνει τις μετρήσεις στο διαδίκτυο σε κάποιον δικό μας server τον οποίο θα ονομάζουμε Network Server (NW Server). Αυτός μετατρέπει τα μηνήματα LoRa Wan σε μηνύματα MQTT τα οποία τα προωθεί σε κάποιον MQTT broker π.χ. mosquitto. Στον ίδιο server ή σε κάποιον άλλο τρέχει το Node Red το οποίο είναι υπεύθυνο για την υλοποίηση της λογικής όλου του συστήματος μέσα από γραφικό προγραμματισμό.<br>
Οι αποφάσεις ακολουθούν αντίθετη κατεύθυνση. Δηλαδή το Node Red δημοσιεύει σε κάποιο topic MQTT το οποίο το παρακολουθεί και ο NW Server. Αυτός μεταφράζει το μήνυμα σε πλαίσιο LoRa Wan το οποίο στέλνει στην πύλη μέσω διαδικτύου. Τέλος η πύλη στέλνει το μήνυμα στον κόμβο αποδέκτη και αυτός εκτελεί μια ενέργεια π.χ. ξεκινάει πότισμα ή μαζεύει την σκίαση.<br>
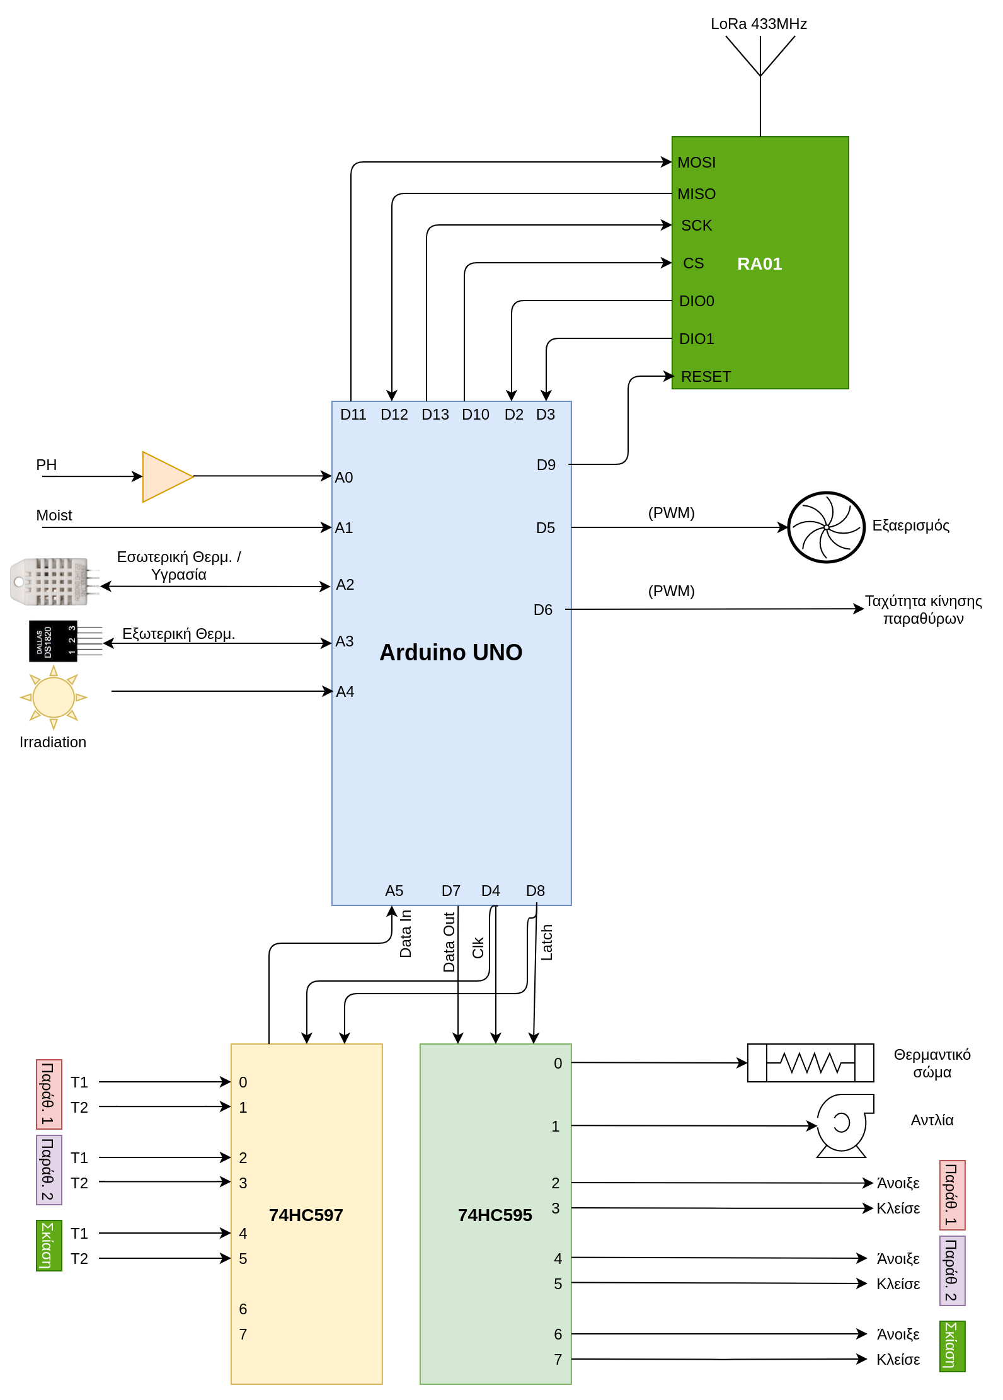
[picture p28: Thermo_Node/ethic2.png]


Η υλοποίηση
===========
Όπως φαίνεται στο παραπάνω διάγραμμα η καρδιά του κόμβου είναι το Node MCU με το ESP8266. Αυτό επικοινωνεί με το LoRa module RA01 ή RA02 μέσω διασύνδεσης SPI. Επειδή το ESP8266 έχει περιορισμένο αριθμό ακροδεκτών, επικοινωνεί μέσω διαύλου I2C με ένα Arduino Uno το οποίο κάνει κάποιες εργασίες χαμηλού επιπέδου, ακολουθώντας τις εντολές του ESP8266. Επειδή και πάλι οι ακροδέκτες δεν επαρκούν, βάλαμε και ένα HC595 ως port expander ώστε να έχουμε επιπλέον 8 ψηφιακές εξόδους.

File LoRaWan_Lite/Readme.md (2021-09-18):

Εδώ υπάρχει ο πηγαίος κώδικας και τα σχέδια του υλικού για το πρωτόκολλο LoRa Wan Lite.

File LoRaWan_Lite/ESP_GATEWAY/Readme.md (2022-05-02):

Εδώ είναι οι κατασκευαστικές οδηγίες και το λογισμικό για την πύλη LoRa Wan Lite ενός καναλιού. Η πύλη μπορεί να βρίσκεται μέχρι 10Km μακριά από τους κόμβους με εξωτερικές κεραίες. Η πύλη είναι υπεύθυνη να προωθεί με διαφάνεια όλα τα πλαίσια LoRa Wan Lite στον NW Server μέσω διαδικτύου.
Το Μάρτιο 2022 πρόσθεσα web interface ώστε να γίνεται ευκολότερα η παραμετροποίηση της πύλης.
Ακολουθούν μερικά στιγμιότυπα από την διεπαφή Web της πύλης





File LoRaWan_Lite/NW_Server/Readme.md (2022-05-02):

Εδώ είναι ο Network Server γραμμένος σε Python 3. Τον Απρίλιο του 2022 έγιναν κάποιες αλλαγές και βελτιώσεις. Υποστηρίζει επιπλέον μηνύματα χωρίς επιβεβαίωση λήψης καθώς και Options στο header του frame. Εκεί μπορούν να υλοποιηθούν διάφορα MAC Commands.
Όταν στέλνει εντολές προς τα nodes και δεν λάβει επιβεβαίωση λήψης απ' αυτούς, επαναλαμβάνει την αποστολή άλλες 2 φορές (σύνολο 3). Την τελευταία φορά εκπέμπει στο παράθυρο TX2 με Data Rate SF12BW125 ώστε να έιναι πιο ευαίσθητος ο δέκτης.

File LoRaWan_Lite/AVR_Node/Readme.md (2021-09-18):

Ο κόμβος LoRa Wan Lite για 8 bit επεξεργαστές τύπου AVR.

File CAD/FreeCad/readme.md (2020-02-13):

Εδώ υπάρχουν τα source αρχεία των τρισδιάστατων μοντέλων φτιαγμένα στο πρόγραμμα FreeCad.

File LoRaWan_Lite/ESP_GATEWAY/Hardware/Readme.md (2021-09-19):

Η πύλη LoRa Wan Lite υποστηρίζει ένα μόνο κανάλι και στην αρχική της έκδοση λειτουργεί αμφίδρομα για κόμβους τάξης Α'. Κατόπιν οδηγίας από τον NW Server μπορεί να εκπέμψει (Download), στο παράθυρο RX1 ή στο RX2 με χαμηλότερο bit rate.
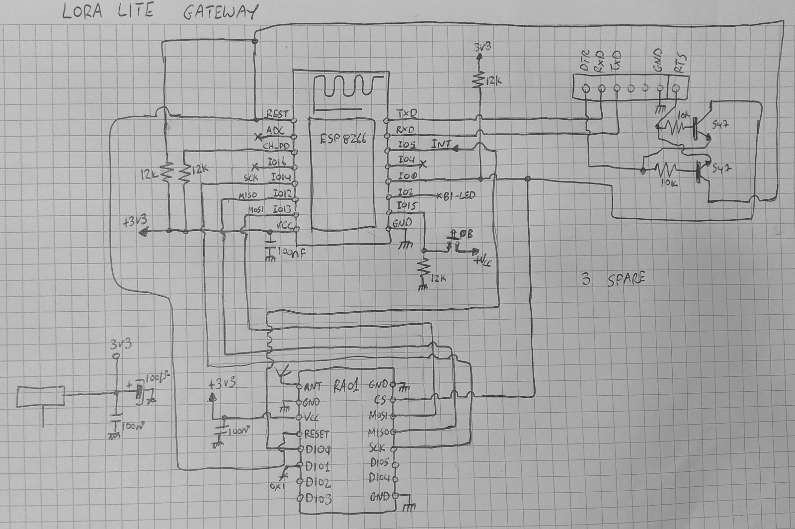
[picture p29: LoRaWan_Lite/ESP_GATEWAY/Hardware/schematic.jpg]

Όπως φαίνεται στο κύκλωμα ο επεξεργαστής ESP8266 επικοινωνεί με το άρθρωμα RA01 μέσω του διαύλου SPI. Ο προγραμματισμός και η εκσφαλμάτωση γίνεται από την σειριακή θύρα. Το ESP8266 επικοινωνεί με το τοπικό δίκτυο ή το διαδίκτυο μέσω του WiFi και του ενσωματωμένου TCP/IP stack.<br>
Η πύλη ακούει συνεχώς στη συχνότητα για εκπομπή από κάποιο κόμβο. Αν λάβει κάτι, χωρίς να αποκρυπτογραφήσει το payload, το ετοιμάζει σε πακέτο JSON και το προωθεί με πρωτόκολλο UDP στον NW Server μέσα από την σύνδεση WiFi.<br>
Ο NW Server λαμβάνει το πακέτο, το αποκρυπτογραφεί και στέλνει το μήνυμα στον MQTT broker. Παράλληλα ετοιμάζει πλαίσιο απάντησης προς τον κόμβο και το στέλνει στη πύλη μέσα της ίδιας σύνδεσης UDP. Το Download πλαίσιο μπορεί να είναι μόνο επιβεβαίωση για το πλαίσιο που μόλις έλαβε, αλλά μπορεί να περιέχει και οδηγίες προς τον κόμβο όπως για παράδειγμα να ανάψει την θέρμανση. <br>
Η πύλη αφού λάβει το πακέτο JSON από τον NW Server, εκπέμπει στο παράθυρο RX1 ή RX2 και ο παραλήπτης κόμβος δέχεται το πλαίσιο.

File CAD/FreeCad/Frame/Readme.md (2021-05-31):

Αρχεία για συνδέσμους κατασκευής πλαισίου.

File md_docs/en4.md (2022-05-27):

<a href="../README.md"><= Επιστροφή</a><br>

<p>Η αρχική ιδέα ήταν να χρησιμοποιήσουμε το πρωτόκολλο LoRa WAN και στο Raspberry να τρέχει τοπικά ο <a href="https://www.chirpstack.io">ChirpStack Network και Application Server</a> που είναι ανοιχτού κώδικα. Εναλλακτικά θα μπορούσαμε να χρησιμοποιήσουμε το <a href="https://www.thethingsnetwork.org/">The Things Network</a> και από εκεί να στέλνουμε τα μηνύματα στον δικό μας MQTT broker. Το ποιο σημαντικό πρόβλημα που παρουσιάστηκε ήταν ότι δεν βρήκαμε έτοιμο firmware πύλης μονού καναλιού που να λειτουργεί ικανοποιητικά ειδικά στο Downlink. Επιπλέον αν βάζαμε το LoRa Wan στους κόμβους έμενε πολύ λίγη ελεύθερη μνήμη. Το πρόβλημα λύνονταν αν βάζαμε πύλη με την πλακέτα <a href="https://wireless-solutions.de/products/lora-solutions-by-imst/radio-modules/ic880a-spi/">iC880A-SPI LoRa® Concentrator</a>, αλλά ανεβάζαμε κατά πολύ το κόστος.</p>
<p>Επειδή εμείς θέλουμε μια απλή υλοποίηση που να λειτουργεί αξιόπιστα με λίγους κόμβους (έως 16) "πειράξαμε" λίγο το πρωτόκολλο LoRa WAN και φτιάξαμε το δικό μας πρωτόκολλο LoRa WAN Lite. Στην πραγματικότητα αφαιρέσαμε δυνατότητες που σε εμάς είναι άχρηστες, π.χ. η διεύθυνση κόμβου από 4 έγινε 2 bytes δηλαδή 65536 κόμβοι. Η σκληρή κρυπτογράφηση AES 128 που έχει το LoRa WAN σε εμάς έγινε μια απλοποιημένη παραλαγή της DES με κλειδιά 64 bit. Το Lora Wan υπστηρίζει 3 τάξεις κόμβων ενώ εμείς έχουμε μόνο κλάση Α.</p>
<p>Με το κομμάτι αυτό δηλαδή ανασχεδιασμό του πρωτοκόλλου και γράψιμο του κώδικα για την πύλη, κόμβους και NW Server, ασχολήθηκε ο καθηγητής μας.</p>
  <p>Εδώ υπάρχει το <a href="https://github.com/stav98/ETHIC/blob/master/resources/documents/LoRa_WAN_Lite_Protocol.pdf">αρχείο με τις προδιαγραφές</a> του πρωτοκόλλου μας.</p>
  <a href="../README.md"><= Επιστροφή</a><br>

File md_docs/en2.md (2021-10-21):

<a href="../README.md"><= Επιστροφή</a><br>

<p>Το υλικό ελέγχου έχει χωριστεί σε τρία μέρη:</p>
  <b>1. Κεντρικός διακομιστής</b>
  <p>Ο διακομιστής μας είναι ένα Raspberry PI 4 στο οποίο θα εγκατασταθούν τα πακέτα: Mosquitto MQTT broker, Node Red και <a href="/LoRaWan_Lite/NW_Server" target="_blank">Network Server</a> το οποίο γράψαμε σε Python 3. Το Raspberry μπορεί να βρίσκεται οπουδήποτε αρκεί να υπάρχει σύνδεση με το διαδίκτυο, να έχουν ανοίξει οι συγκεκριμένες πόρτες του router και να κατευθύνονται στο Raspberry. Επίσης αν έχουμε δυναμική απόδοση διεύθυνσης IP, πρέπει να φαίνεται στον έξω κόσμο μέσω κάποιου παρόχου δυναμικού DNS π.χ. FreeDNS, DynDNS κλπ. Εναλλακτικά μπορούμε να βάλουμε ένα PC με Linux ή να νοικιάσουμε κάποιο VPS με Linux.</p>
  <b>2. Πύλη επικοινωνίας LoRa</b>
  <p>Η <a href="/LoRa_GateWay">πύλη LoRa</a> είναι μια διαφανής πύλη η οποία λαμβάνει πλαίσια LoRa WAN από τους ελεγκτές θερμοκηπίων - κόμβους και τα προωθεί στο διαδίκτυο και συγκεκριμένα στο Raspberry Pi 4 ή τον διακομιστή τον οποίο στήσαμε στην προηγούμενη παράγραφο. Επίσης παίρνει πακέτα από τον διακομιστή και τα προωθεί στους ελεγκτές - κόμβους. Η πύλη τοποθετείται οπουδήποτε αρκεί να έχει πρόσβαση στο διαδίκτυο. Επειδή τα θερμοκήπια μπορεί να είναι αρκετά μακριά, η πύλη μπορεί να εγκατασταθεί στο σπίτι του παραγωγού.</p>
  <b>3. Ελεγκτής θερμοκηπίου - Κόμβος</b>
<p>Οι κόμβοι μπορούν να βρίσκονται σε διαφορετικά μέρη και σε απόσταση μέχρι 20Km (με εξωτερικές κεραίες) από την πύλη αρκεί να μην υπάρχουν πολλά φυσικά εμπόδια όπως κτίρια ή βουνά.</p>

<a href="../README.md"><= Επιστροφή</a><br>

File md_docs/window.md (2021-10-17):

<a href="../README.md"><= Επιστροφή</a><br>

<p>Τα παράθυρα είναι κατασκευασμένα από πόρτες οδηγών CD-ROM και ανοιγοκλείνουν ανεξάρτητα. Αν χρειαστεί να πέσει η θερμοκρασία εντός του θερμοκηπίου, τότε τα παράθυρα ανοίγουν. Αν έξω επικρατεί ψύχος τότε τα παράθυρα κλείνουν. Λειτουργούν με τάση 5V και ρυθμίζεται η ταχύτητα κίνησης. Επιπλέον μπορούν να είναι σε ενδιάμεσες καταστάσεις π.χ. ανοιχτά κατά το 1/5.</p>
  
<p>Ακολουθεί video με την λειτουργία των παραθύρων:</p>
  <p align="center">
</p>
  <a href="../README.md"><= Επιστροφή</a><br>

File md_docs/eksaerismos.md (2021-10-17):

<a href="../README.md"><= Επιστροφή</a><br>

<p>Το σύστημα εξαερισμού αποτελείται από δύο ανεμιστήρες από PC που λειτουργούν στα 12V. Ο ένας εισάγει αέρα απ' έξω ενώ ο απέναντι βγάζει τον ζεστό αέρα του θερμοκηπίου. Το λογισμικό μπορεί να ρυθμίζει την ταχύτητα περιστροφής των ανεμιστήρων ανάλογα με την θερμοκρασία.</p>
  
<p>Ακολουθεί video με την λειτουργία του εξαερισμού:</p>
  <p align="center">
</p>
  <a href="../README.md"><= Επιστροφή</a><br>

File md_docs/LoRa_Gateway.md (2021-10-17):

<a href="../README.md"><= Επιστροφή</a><br>

  Η πύλη LoRa Wan Lite υποστηρίζει ένα μόνο κανάλι και στην αρχική της έκδοση λειτουργεί αμφίδρομα για κόμβους τάξης Α'. Κατόπιν οδηγίας από τον NW Server μπορεί να εκπέμψει (Download), στο παράθυρο RX1 ή στο RX2 με χαμηλότερο bit rate.

Όπως φαίνεται στο κύκλωμα ο επεξεργαστής ESP8266 επικοινωνεί με το άρθρωμα RA01 μέσω του διαύλου SPI. Ο προγραμματισμός και η εκσφαλμάτωση γίνεται από την σειριακή θύρα. Το ESP8266 επικοινωνεί με το τοπικό δίκτυο ή το διαδίκτυο μέσω του WiFi και του ενσωματωμένου TCP/IP stack.<br>
Η πύλη ακούει συνεχώς στη συχνότητα για εκπομπή από κάποιο κόμβο. Αν λάβει κάτι, χωρίς να αποκρυπτογραφήσει το payload, το ετοιμάζει σε πακέτο JSON και το προωθεί με πρωτόκολλο UDP στον NW Server μέσα από την σύνδεση WiFi.<br>
Ο NW Server λαμβάνει το πακέτο, το αποκρυπτογραφεί και στέλνει το μήνυμα στον MQTT broker. Παράλληλα ετοιμάζει πλαίσιο απάντησης προς τον κόμβο και το στέλνει στη πύλη μέσα της ίδιας σύνδεσης UDP. Το Download πλαίσιο μπορεί να είναι μόνο επιβεβαίωση για το πλαίσιο που μόλις έλαβε, αλλά μπορεί να περιέχει και οδηγίες προς τον κόμβο όπως για παράδειγμα να ανάψει την θέρμανση. <br>
Η πύλη αφού λάβει το πακέτο JSON από τον NW Server, εκπέμπει στο παράθυρο RX1 ή RX2 και ο παραλήπτης κόμβος δέχεται το πλαίσιο.
  
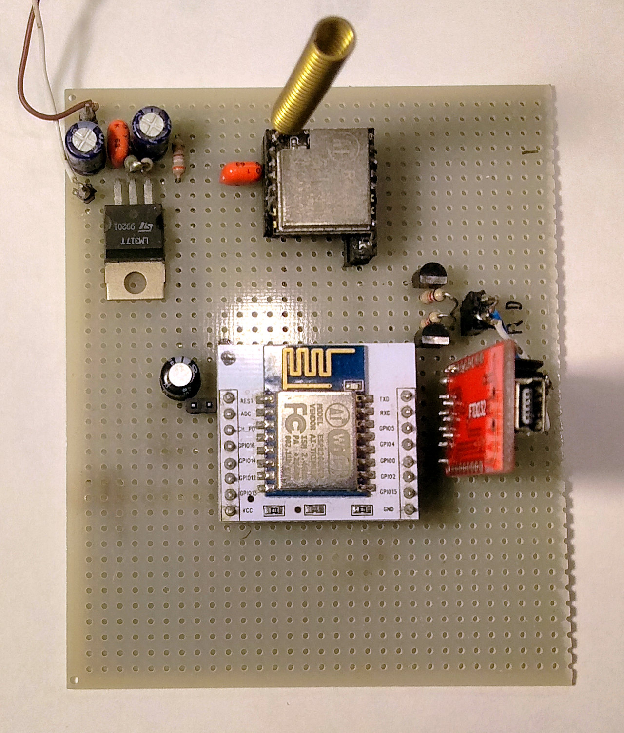
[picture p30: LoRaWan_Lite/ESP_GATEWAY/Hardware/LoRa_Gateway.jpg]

<a href="../README.md"><= Επιστροφή</a>

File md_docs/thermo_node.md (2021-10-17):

<a href="../README.md"><= Επιστροφή</a><br>

<p>Ο ελεγκτής του θερμοκηπίου είναι κατασκευασμένος με το Arduino UNO και πάνω σ' αυτό μπαίνουν δύο πρωτότυπες κάρτες επέκτασης συναρμολογημένες σε perfboard. Η πρώτη και μεγαλύτερη έχει όλα τα εξαρτήματα για την διασύνδεση των αισθητήρων και ενεργοποιητών του θερμοκηπίου. Από πάνω υπάρχει ο πομποδέκτης LoRa για την επικοινωνία με την πύλη LoRa WAN Lite.</p>
  
<p>Παρακάτω φαίνονται τα θεωρητικά κυκλώματα των δύο πλακετών.</p>
<p>Πρώτη πλακέτα.</p>
  
<p>Δεύτερη πλακέτα.</p>
  
<p>Χαρακτηρισμός συνδετήρων.</p>

  <a href="../README.md"><= Επιστροφή</a><br>

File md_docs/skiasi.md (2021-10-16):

<a href="../README.md"><= Επιστροφή</a><br>

<p>Το σύστημα σκίασης αποτελείται από δύο κουρτίνες μήκους 60cm έκαστη. Είναι κατασκευασμένο από λαμαρίνα και ηλεκτρολογικούς σωλήνες PVC. Οι σωλήνες λειτουργούν ως οδηγοί στους οποίους κινούνται οι κουρτίνες. Η κίνηση δίνεται από ένα κινητήρα DC 12V με μειωτήρες και μεταδίδεται από ένα σύστημα ιμάντων οι οποίοι έχουν φτιαχτεί από σαμπρέλα ποδηλάτου. Στο πρώτο τμήμα υπάρχουν δύο τερματικοί διακόπτες οι οποίοι ειδοποιούν το Arduino αν η κουρτίνες είναι απλωμένες ή μαζεμένες ώστε να σταματάει την περιστροφή του κινητήρα.</p>
  
<p>Αρχικά στραντζάραμε την λαμαρίνα στη στράντζα του μηχανουργείου και μετά κάναμε οπές για να περάσουν οι οδηγοί.</p>
  
  
  
  

<p>Ακολουθεί video:</p>
  <p align="center">

</p>
<p>Video με τις δοκιμές λειτουργίας της σκίασης:</p>
  <p align="center">

</p>
  <a href="../README.md"><= Επιστροφή</a><br>

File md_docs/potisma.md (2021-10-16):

<a href="../README.md"><= Επιστροφή</a><br>

<p>Τα φυτά μας μεγαλώνουν σε υπόστρωμα πετροβάμβακα το οποίο είναι αδρανές υλικό. Με μικρά ακροφίσια (beck), τροφοδοτούμε τις ρίζες με νερό, μέσα στο οποίο είναι διαλυμένες οι θρεπτικές ουσίες τις οποίες τις εισάγουμε με λιπάσματα. Από κάτω, στο νάιλον το οποίο περιβάλει τον πετροβάμβακα, έχουμε κάνει οπές ώστε το περίσσευμα νερού να πέφτει στο παρτέρι.</p>
  
<p>Όπως φαίνεται στο παραπάνω σκαρίφημα, τα παρτέρια είναι κατασκευασμένα από σωλήνα αποχέτευσης PVC Φ160 κομμένη εγκάρσια στα 3/5 της διαμέτρου. Στο δάπεδο υπάρχει ηλεκτρολογικό κανάλι το οποίο στηρίζει το υπόστρωμα ώστε να μην παραμορφωθεί από το βάρος όταν βραχεί και επιπλέον να γίνεται και αποστράγγιση του νερού. Στα παρτέρια δίνεται μέγιστη κλίση 3% ώστε αν το νερό ξεπεράσει την στάθμη να μπορεί να επιστρέψει πίσω στη δεξαμενή.</p>
  
<p>Η δεξαμενή με το θρεπτικό διάλυμα τοποθετείται χαμηλότερα από την μακέτα και με μια αντλία στέλνει το νερό στις ρίζες των φυτών.</p>
  
  
  
  
<p>Ακολουθεί video με τις δοκιμές ποτίσματος:</p>
  <p align="center">

</p>
  <a href="../README.md"><= Επιστροφή</a><br>

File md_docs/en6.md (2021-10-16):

<a href="../README.md"><= Επιστροφή</a><br>

<p>Για να κατανοήσουμε καλύτερα τις λειτουργίες της άρδευσης και του συστήματος σκίασης, επισκεφθήκαμε ένα κοντινό θερμοκήπιο υδροπονικής καλλιέργειας. Ευχαριστούμε πολύ τον παραγωγό κ. Γιώργο Κολλίτση για την αναλυτική παρουσίαση της λειτουργίας του θερμοκηπίου του.</p>
  
  
  <a href="../README.md"><= Επιστροφή</a><br>

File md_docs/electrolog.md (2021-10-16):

<a href="../README.md"><= Επιστροφή</a><br>

<p>Ακολούθησε η τοποθέτηση των συσκευών (αισθητήρων και ενεργοποιητών) και έγινε η ηλεκτρολογική εγκατάσταση.</p>
  
  
  
  
<p>Μετά τοποθετήσαμε το νάιλον της οροφής. Η οροφή είναι ανοιγόμενη ώστε να είναι ευκολότερη η πρόσβαση στο εσωτερικό του θερμοκηπίου. Τα πλαϊνά νάιλον θα τοποθετηθούν όταν τελειώσουν όλες οι εργασίες.</p>
  
  

  <a href="../README.md"><= Επιστροφή</a><br>

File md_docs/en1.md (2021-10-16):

<a href="../README.md"><= Επιστροφή</a><br>

<p>Το θερμοκήπιο έχει διαστάσεις 120cm (μήκος) x 60cm (πλάτος) x 95cm (ύψος) και ο σκελετός είναι κατασκευασμένος από PVC ηλεκτρολογικά κανάλια βαρέως τύπου διαμέτρου 20mm. Το υλικό αυτό το επιλέξαμε γιατί είναι ελαφρύ, πολύ ανθεκτικό και κατεργάζεται εύκολα. Η όλη κατασκευή είναι στερεωμένη σε μοριοσανίδα 16mm, ώστε να μεταφέρεται εύκολα από δύο άτομα. Στο εσωτερικό περιέχει δύο παρτέρια μήκους 110cm όπου εκεί θα φυτευτούν 16 ρίζες από τα φυτά που πρόκειται να καλλιεργηθούν.<br>
  Ο σκελετός ντύνεται με διάφανο νάιλον ώστε να περνάει το ηλιακό φως.</p>
  
Οι λειτουργίες που γίνονται μέσα στο θερμοκήπιο είναι οι παρακάτω:<br>
  <b>1. Πότισμα</b>
  <p>Σε χαμηλότερο επίπεδο υπάρχει δεξαμενή χωρητικότητας 20-30lt με το νερό και τις θρεπτικές ουσίες. Με μία αντλία πλυντηρίου το νερό ανεβαίνει πάνω και με σταγόνες ποτίζει τα φυτά μέσα από 16 ακροφύσια. Αυτόματα όταν το νερό ξεπεράσει την επιτρεπτή στάθμη δίνεται εντολή ώστε να σταματήσει η αντλία. Αν για κάποιο λόγο το νερό υπερχειλίσει, τότε με την αρχή των συγκοινωνούντων δοχείων, επιστρέφει πίσω στη δεξαμενή. Επίσης μέσα στο υπόστρωμα πετροβάμβακα έχει τοποθετηθεί πεχάμετρο ώστε να ελέγχουμε το ph του διαλύματος.</p>
  <b>2. Εξαερισμός</b>
  <p>Ο εξαερισμός γίνεται με δύο τρόπους:<br> Α) Με παράθυρα στο ψηλότερο σημείο της οροφής. Αυτά είναι κατασκευασμένα από δύο παλιούς οδηγούς CD-ROM που έχουν αφαιρεθεί όλα τα εξαρτήματα εκτός από τον μηχανισμό της πόρτας και λειτουργούν σαν συρόμενα παράθυρα. Αυτά ανοίγουν και κλείνουν ώστε να ρυθμίζεται η εσωτερική θερμοκρασία.<br> Β) Με δύο ανεμιστήρες από τροφοδοτικά παλιών υπολογιστών, οι οποίοι κάνουν βεβιασμένη κυκλοφορία αέρα. (Ο ένας ωθεί μέσα και ο απέναντι βγάζει τον αέρα έξω). Με τον έλεγχο των στροφών κρατάμε την θερμοκρασία και την υγρασία στα επιθυμητά επίπεδα. Μέσα στο θερμοκήπιο υπάρχει θερμόμετρο και υγρασιόμετρο ώστε να ελέγχονται αυτά τα μεγέθη κάθε ένα λεπτό.</p>
  <b>3. Σκίαση</b>
<p>Στην οροφή υπάρχει σύστημα κουρτινών σκίασης. Αποτελείται από δύο μέρη και απλώνει ή μαζεύει ανάλογα με την ένταση του ηλιακού φωτός. Στην οροφή εξωτερικά υπάρχει ένα μικρό φωτοβολταϊκό το οποίο μετράει την ένταση της ηλιακής ακτινοβολίας. Αν η ένταση ξεπεράσει τα επιτρεπτά επίπεδα, οι κουρτίνες απλώνουν ώστε να προστατέψουν τα φυτά. Όταν είναι νύχτα και έξω επικρατεί παγετός, οι κουρτίνες απλώνουν ώστε να μικρύνει ο χώρος και να μην χάνεται θερμότητα από την οροφή. Αν τώρα έξω έχει πολύ ηλιοφάνεια και η θερμοκρασία μέσα έχει ξεπεράσει τα επιτρεπτά επίπεδα, η κουρτίνες μαζεύουν σε βήματα ώστε να μην μπαίνει μέσα πολύ φως αλλά και να μπορεί να φύγει ο ζεστός αέρας από τα παράθυρα της οροφής.</p> 
  <b>4. Θέρμανση - Φωτισμός</b>
<p>Για θερμαντικό σώμα χρησιμοποιούμε δύο λαμπτήρες πυρακτώσεως των 100W οι οποίοι ζεσταίνουν τον χώρο του θερμοκηπίου όταν έξω επικρατεί παγετός. Επίσης φωτίζουν τα φυτά τη νύχτα ώστε να γίνεται φωτοσύνθεση και να αναπτύσσονται γρηγορότερα.</p>
<a href="../README.md"><= Επιστροφή</a><br>

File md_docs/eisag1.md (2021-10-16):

<a href="../README.md"><= Επιστροφή</a><br>
  
Εισαγωγή - Θεωρητικό υπόβαθρο
=============================

**Τι είναι η Υδροπονία;**

Η υδροπονία είναι η πλέον τεχνολογικά εξελιγμένη μέθοδος καλλιέργειας θερμοκηπιακών μονάδων, με αυξημένες απαιτήσεις σε επίπεδο εξοπλισμού  και γνώσεων του καλλιεργητή. Οι υδροπονικές καλλιέργειες εξασφαλίζουν υψηλές στρεμματικές αποδόσεις  κατά τη λειτουργία του θερμοκηπίου, μείωση κόστους παραγωγής και ανταγωνιστικά προϊόντα υψηλής και σταθερής ποιότητας.

**Πλεονεκτήματα της Υδροπονίας**

Με την Θερμοκηπιακή Υδροπονία μπορούμε να ελαχιστοποιήσουμε την εποχικότητα στην παραγωγή, και να εξασφαλίσουμε σταθερή και ποιοτική παραγωγή προϊόντων σε σταθερές και ελεγχόμενες συνθήκες. Η Θερμοκηπιακή Υδροπονία δεν έχει ανάγκη από χώμα και μπορεί να χρησιμοποιηθεί σε μέρη όπου η καλλιέργεια στο χώμα είναι αδύνατη (άγονα–πετρώδη εδάφη).
Επιτυγχάνει σημαντική εξοικονόμηση νερού, δεν μολύνει το περιβάλλον και δεν απαιτεί ζιζανιοκτόνα. 
Συγχρόνως πετυχαίνουμε αύξηση της παραγωγής από 3 έως 10 φορές περισσότερο από την παραδοσιακή καλλιέργεια.

Το μεγαλύτερο όφελος της υδροπονικής καλλιέργειας είναι η ριζική αντιμετώπιση των εδαφογενών ασθενειών. Η καλλιέργεια εκτός εδάφους καθιστά περιττή την απολύμανση του εδάφους με τη χρήση χημικών ουσιών. Συνεπώς οι καλλιέργειες εκτός εδάφους είναι απαλλαγμένες από την παρουσία παθογόνων στο ριζικό περιβάλλον, όταν πραγματοποιούνται είτε σε καθαρό θρεπτικό διάλυμα είτε σε υπόστρωμα που χρησιμοποιείται για πρώτη φορά. Ένα άλλο πλεονέκτημα των υδροπονικών καλλιεργειών είναι η μείωση του κόστους θέρμανσης λόγω της κάλυψης του εδάφους η οποία οδηγεί σε μειωμένη εξάτμιση νερού και συνεπώς στον περιορισμό της κατανάλωσης ενέργειας σε μορφή λανθάνουσας θερμότητας. Μειωμένο κόστος θέρμανσης προκύπτει επίσης και από το γεγονός ότι οι υδροπονικές καλλιέργειες δεν εξαρτώνται από τη θερμοκρασία του εδάφους του θερμοκηπίου. Ένα άλλο πλεονέκτημα είναι η σημαντική πρωίμιση της παραγωγής που οφείλεται κυρίως στις υψηλότερες θερμοκρασίες που μπορούν να διατηρηθούν στο περιβάλλον των ριζών.

**Συνοπτικά θα μπορούσαμε να πούμε ότι:**
1. Η Θερμοκηπιακή Υδροπονία αποτελεί μια άριστη εναλλακτική λύση αντιμετώπισης των προβλημάτων που προκαλούν οι μεταδιδόμενες μέσω του εδάφους ασθένειες (π.χ. φουζάριο, βερτιτσίλιο, πύθιο κ.τ.λ.), ενώ το ξεκίνημα της καλλιέργειας γίνεται με απουσία παθογόνων στο ριζικό περιβάλλον.

2. Απαλλαγή της φυτείας από την παρουσία ζιζανίων.

3. Λύνεται το πρόβλημα της χαμηλής γονιμότητας που εμφανίζουν πολλά εδάφη, είτε λόγω της υπερεντατικής τους εκμετάλλευσης και της μονοκαλλιέργειας, είτε λόγω δυσμενών φυσικών ιδιοτήτων (π.χ. εναλατωμένα εδάφη, πολύ βαριά εδάφη, εδάφη με πολύ χαμηλή περιεκτικότητα σε οργανική ουσία).

4. Έχει αποδειχθεί στην πράξη ότι η καλλιέργεια πάνω σε καλής ποιότητας υποστρώματα και σε καθαρό θρεπτικό διάλυμα επιφέρει σημαντική πρωίμιση της συγκομιδής. Αυτό οφείλεται στη δυνατότητα διατήρησης υψηλότερων θερμοκρασιών στον χώρο του ριζοστρώματος.

5. Η καλλιέργεια των φυτών εκτός εδάφους απαλλάσσει τον καλλιεργητή, αφενός, από τις εργασίες της προετοιμασίας του εδάφους (όργωμα, φρεζάρισμα, βασική λίπανση κ.τ.λ.), με αποτέλεσμα να μειώνονται οι ανάγκες σε εργατικά, και, αφετέρου, να είναι δυνατή η φύτευση νέας καλλιέργειας αμέσως μετά την απομάκρυνση της προηγούμενης.

6. Δίνει αυξημένες αποδόσεις λόγω της αύξησης της πυκνότητας φύτευσης, της άριστης θρέψης, της δυνατότητας διατήρησης υψηλότερων θερμοκρασιών στο ριζόστρωμα κατά τη διάρκεια της ψυχρής εποχής του έτους και των καλύτερων φυσικοχημικών ιδιοτήτων, που έχουν τα υποστρώματα έναντι του εδάφους.

7. Αυτοματοποίηση και μηχανοποίηση των καλλιεργητικών εργασιών.
<br>
<a href="../README.md"><= Επιστροφή</a><br>

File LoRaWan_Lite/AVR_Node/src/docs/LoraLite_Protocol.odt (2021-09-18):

Πλευρά δικτύου

Κάθε Gateway έχει ένα GW-ID το οποίο είναι 8 bytes και προκύπτει από το MAC του WiFi παρεμβάλλοντας FF FF στη μέση. Δηλαδή αν το MAC είναι 18:FE:34:D1:71:7B θα προσθέσω στη μέση τα FF FF και θα γίνει 18:FE:34:FF:FF:D1:71:7B.

Μηνύματα PULL_DATA

Περιοδικά π.χ. κάθε 30 sec ή πύλη στέλνει μηνύματα PULL_DATA στον server με πρωτόκολλο UDP και αυτός απαντάει με PULL_RESP. Τα μηνύματα αυτά κρατούν ανοιχτά τα firewalls τα οποία προστατεύουν την πύλη.

Ένα PULL_DATA μήνυμα έχει μήκος 12 bytes και είναι της μορφής:

Μήκος (bytes) | 1 | 2 | 1 | 8
Περιγραφή | Protocol Version | Κουπόνι τυχαία τιμή | Αναγνωριστικό PULL_DATA | GW-ID
Δεδομένα | 0x01 | XX, XX | 0x02

Μόλις λάβει το μήνυμα ο Server, θα απαντήσει αμέσως με PULL_ACK μήνυμα το οποίο έχει μήκος 12 bytes και την παρακάτω μορφή:

Μήκος (bytes) | 1 | 2 | 1 | 8
Περιγραφή | Protocol Version | Η τιμή του κουπονιού που επιβεβαιώνεται | Αναγνωριστικό PULL_ACK | GW-ID
Δεδομένα | 0x01 | XX, XX | 0x04

Μηνύματα PUSH_DATA

Μόλις η πύλη λάβει ένα έγκυρο πακέτο LoRa-Lite αμέσως θα το προωθήσει στον server με μήνυμα PUSH_DATA το οποίο έχει μεταβλητό μήκος.

Μήκος (bytes) | 1 | 2 | 1 | 8 | Μεταβλητό μήκος
Περιγραφή | Protocol Version | Κουπόνι τυχαία τιμή | Αναγνωριστικό PUSH_DATA | GW-ID | Αντικείμενο JSON
Δεδομένα | 0x01 | XX, XX | 0x00 | | {"rxpk": [{"data": "ADGrrAABTNAwam66O/8uYTRqbYVYThJinmptkReBBmqAam2JEZ9mayBqbYkx/iF45mptkCZ+zpJoa5GAZkFdKQ==", "time": "2020-10-21T17:23:21.881Z", "chan": 0, "tmst": 507831862, "stat": 1, "modu": "LORA", "lsnr": 9, "rssi": -101, "rfch": 1, "codr": "4/5", "freq": 433.175, "datr": "SF7BW125", "size": 64}]}

Μόλις λάβει το μήνυμα ο Server, θα απαντήσει αμέσως με PUSH_ACK μήνυμα το οποίο έχει μήκος 4 bytes και την ακόλουθη μορφή:

Μήκος (bytes) | 1 | 2 | 1
Περιγραφή | Protocol Version | Η τιμή του κουπονιού που επιβεβαιώνεται | Αναγνωριστικό PULL_ACK
Δεδομένα | 0x01 | XX, XX | 0x01

Αντικείμενα JSON

Τα αντικείμενα JSON (JavaScript Object Notation) χρησιμοποιούνται για το upstream από τη πύλη προς server και είναι τα παρακάτω:

{

"rxpk":[ {...}, ...], //πίνακας για πολλά

"rxpk":{...}, //ή ένα

"stat":{...},

"other":{...},

"other1":value

}

rxpk:

Όνομα | Τύπος | Λειτουργία | Παρατηρήσεις
data | String | Η καθαρή πληροφορία κωδικοποιημένη σε Base64
time | String | Ο χρόνος UTC που η πύλη έλαβε το πακέτο
chan | Unsigned integer | Το κανάλι στο οποίο έγινε η λήψη του πακέτου
tmst | Unsigned integer (32bit) | Ο χρόνος του εσωτερικού χρονιστή της πύλης κατά τον οποίο έγινε λήψη του πακέτου σε micros.
stat | integer | Το αποτέλεσμα από τον έλεγχο checksum της πύλης. 1 = σωστό -1 = λάθος 0 = δεν έγινε έλεγχος
modu | String | LoRa ή FSK
lsnr | Float | Ο λόγος SNR σε db
rssi | integer | Η ένταση σήματος σε dBm
rfch | Unsigned integer
codr | String | Αν είναι LoRa το Code Rate π.χ. 4/5
freq | Unsigned float | Η συχνότητα λήψης σε MHz π.χ. 433.175
datr | String | Το data rate για LoRa π.χ. SF7BW125
size | Unsigned integer | Το μήκος του ληφθέντος πλαισίου σε bytes.

Stat:

Επίσης χρησιμοποιούνται για το downstream από server προς πύλη και είναι το εξής:

{

"txpk":{...}

}

Πλευρά Radio

Radio PHY επίπεδο

Preable | PHDR | PHDR_CRC | PHYPayload | CRC*

* Το CRC υπάρχει μόνο στα μηνύματα uplink (από κόμβο σε πύλη).

Τα ροζ πεδία υλοποιούνται από το LoRa chipset.

Το PHYPayload αποτελείται από τρία μέρη:

  1. MHDR (MAC Header) με μήκος 1 byte.
  2. MACPayload με μεταβλητό μήκος.
  3. MIC (Message Integrity Check) με μήκος 2 bytes.

MHDR

7 | 6 | 5 | 4 | 3 | 2 | 1 | 0
MTYPE | | ADR | ACK | F-PENDING | OPTIONS LENGTH

MTYPE:

00 : Μήνυμα χωρίς επιβεβαίωση Up (Κόμβος προς πύλη)

01 : Μήνυμα χωρίς επιβεβαίωση Down (Πύλη προς κόμβο)

10 : Μήνυμα με επιβεβαίωση Up

11 : Μήνυμα με επιβεβαίωση Down

Ένα μήνυμα χωρίς επιβεβαίωση δεν απαιτεί από τον δέκτη να επιβεβαιώσει τη λήψη, ενώ ένα μήνυμα με επιβεβαίωση ζητάει να απαντήσει ο δέκτης με ACK.

ADR : Adaptive Data Rate

ACK : Επιβεβαίωση λήψης

F-Pending : Μόνο για Down (Πύλη προς κόμβο) για να ειδοποιήσει ότι έχει να στείλει και άλλα δεδομένα ώστε ο κόμβος να κάνει Uplink κάτι, ώστε να ανοίξει και άλλο Rx παράθυρο και να πάρει τα δεδομένα από τη πύλη.

OPTIONS LENGTH : Το μήκος ειδικών εντολών MAC Commands π.χ. αλλαγή καναλιού ή Data Rate από 0 – 7 (8). Οι εντολές ακολουθούν στο πεδίο Fopts του MACPayload.

MACPayload

Αποτελείται από τα:

  1. FHDR (Frame Header)
  2. PAYLOAD κρυπτογραφημένο

FHDR

DEV ADDR (2) | FRAME COUNT (2) | Fopts (0-7) | Fport (1)
Διεύθυνση συσκευής | Αύξων αριθμός | Options | Πόρτα

Αν η πόρτα Fport είναι 0 τότε στο Payload βάζουμε MAC Commands, το Fopt είναι κενό και το OPTIONS LENGTH είναι 0.

PAYLOAD είναι το καθαρό μήνυμα κωδικοποιημένο με αλγόριθμο DES.

MIC

Είναι checksum των 2 bytes στο οποίο υπολογίζονται όλα τα προηγούμενα.






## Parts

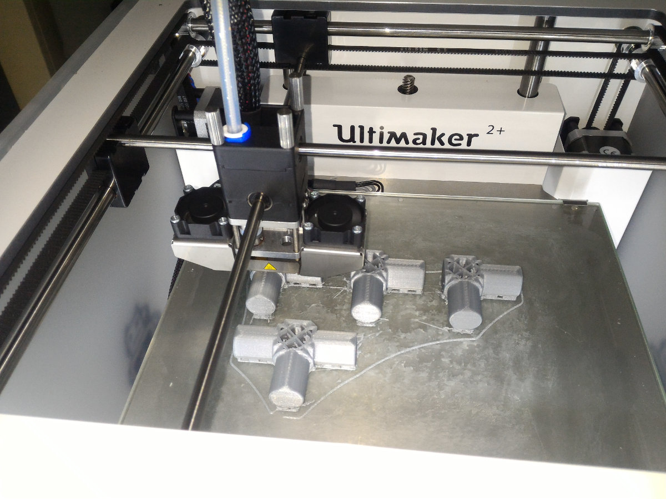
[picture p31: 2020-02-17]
resources/images/3d_parts4.jpg

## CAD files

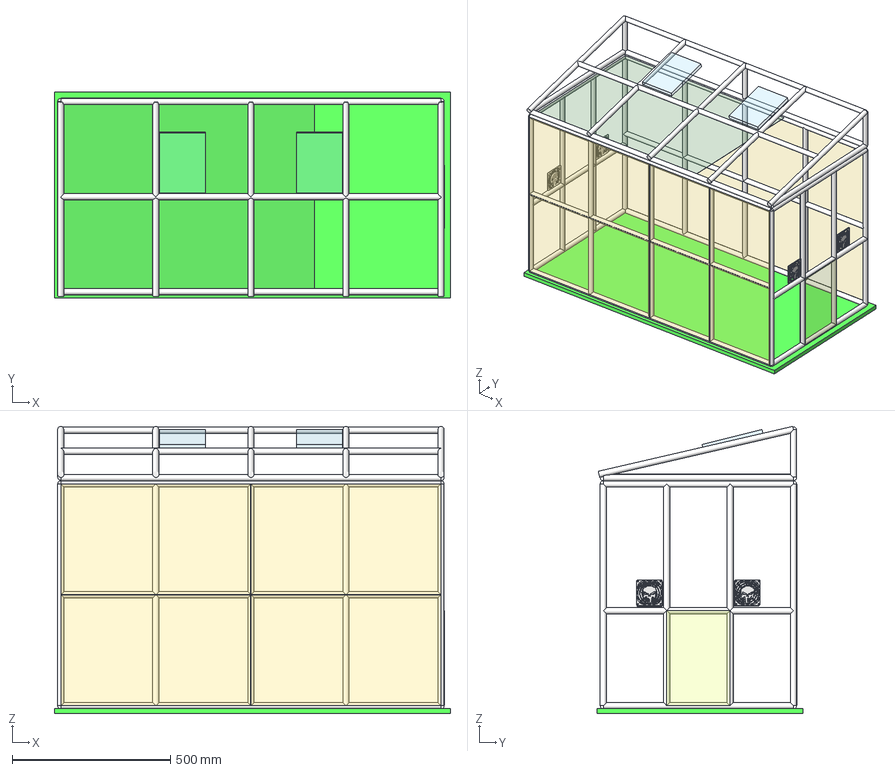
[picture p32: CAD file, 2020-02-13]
CAD/FreeCad/frame.fcstd
1250.0 x 650.0 x 906.7 mm
tube120b
tube60l
tube60r
tube120f
Basement
tubev800fr
tubev800fl
tubev800fc1
tubev800fc2
tubev800fc3
tube120fu
tube120f001
tubev800bl
tubev800br
tubev800bc1
tubev800bc2
tubev800bc3
tube120bu
tube120b001
tube60lu
tube60l001
tubev800bl003
tubev800bl004
tube60ru
tubedoorR1
tubedoorR2
tubedoorRu
DoorR
tube60lu001
tube60ru001
tube120fu001
tube120bu001
tubev800bl001
tubev800bl002
tube120bu002
tube60lu-plag
tube60ru-plag
tube60lu-plag001
Window1
tube60lu-plag002
tube60lu-plag003
Window002
tube120bu003
tubev800bl005
Skin_F
Skin_B
Kourtina
Punisher_Fan_Shield_-_80mm001
Punisher_Fan_Shield_-_80mm
Punisher_Fan_Shield_-_80mm002
Punisher_Fan_Shield_-_80mm003

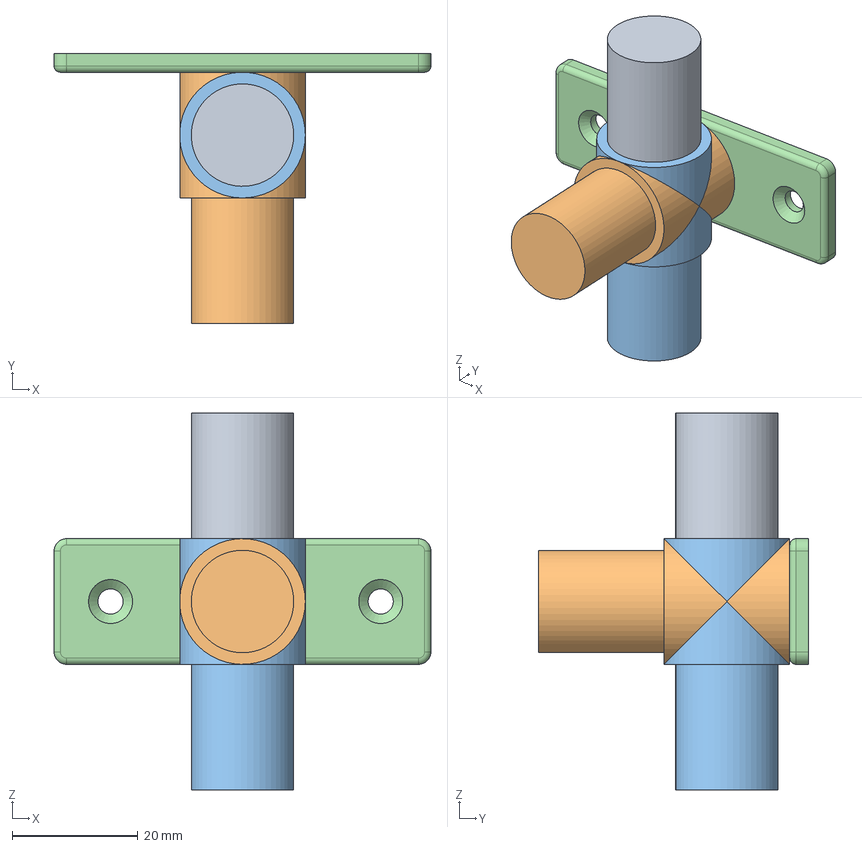
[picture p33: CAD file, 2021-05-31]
CAD/FreeCad/Frame/goniaT_w_base.FCStd
60.0 x 43.0 x 60.0 mm

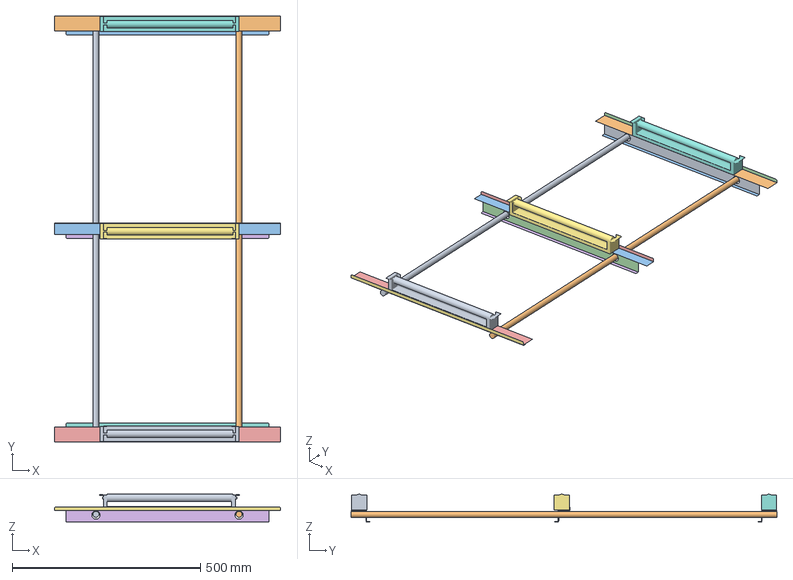
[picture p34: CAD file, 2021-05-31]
CAD/FreeCad/skiasi/kourtina.fcstd
600.0 x 1130.8 x 73.5 mm
Cube004 (Mirror #1)
Cut003 (Mirror #2)
Chamfer005 (Mirror #3)
Chamfer007 (Mirror #4)
T16_120-00
T16_12-01
troxalia_base
troxalia_base001
troxalia_base002

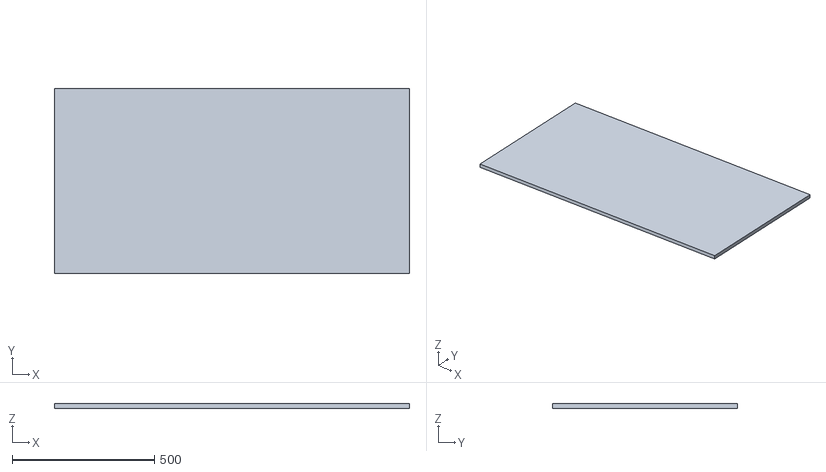
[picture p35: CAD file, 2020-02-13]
CAD/STL/base.stl
1250.0 x 650.0 x 16.0

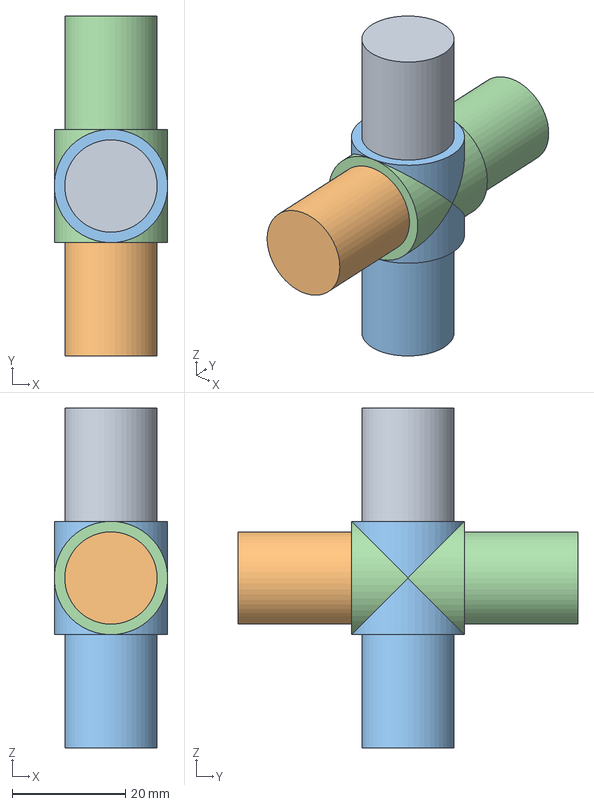
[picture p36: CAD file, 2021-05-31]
CAD/FreeCad/Frame/gonia+.FCStd
20.0 x 60.0 x 60.0 mm

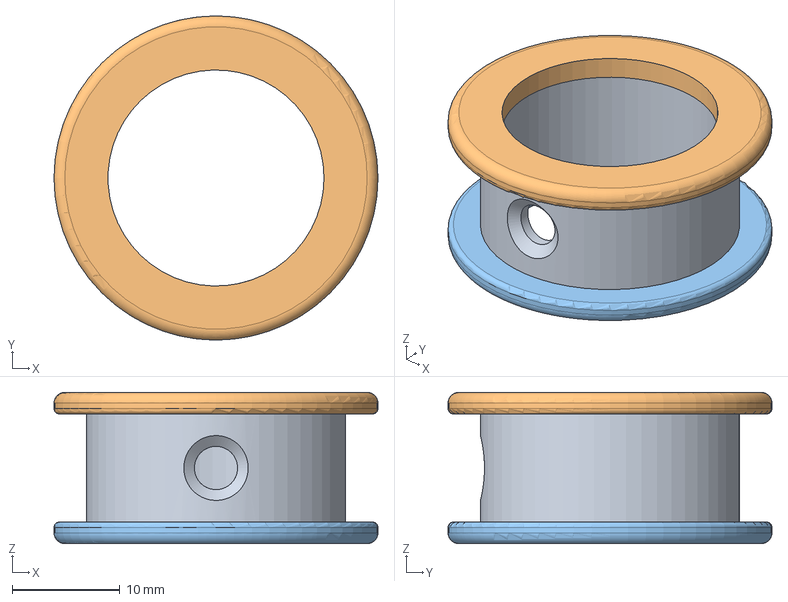
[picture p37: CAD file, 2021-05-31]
CAD/FreeCad/skiasi/troxalia.fcstd
30.0 x 30.0 x 14.0 mm

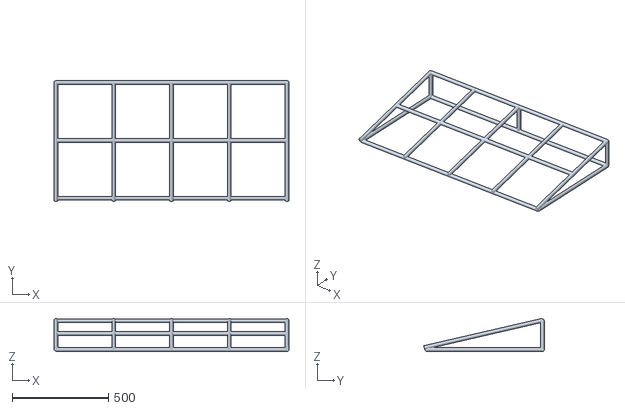
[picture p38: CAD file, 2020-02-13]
CAD/STL/roof.stl
1220.0 x 626.1 x 171.7

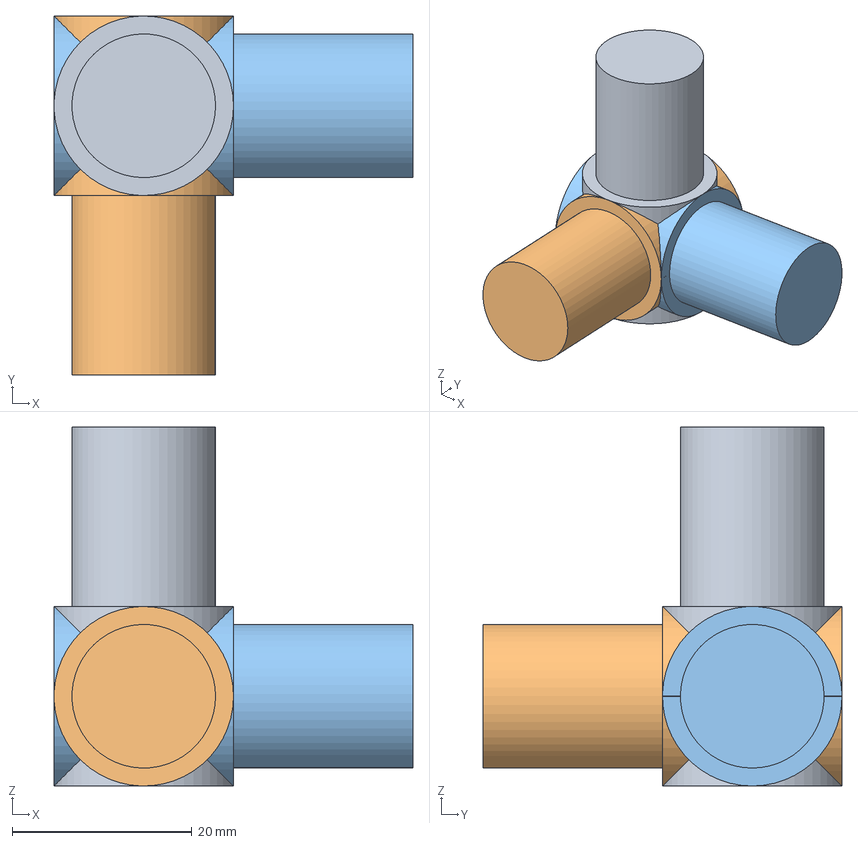
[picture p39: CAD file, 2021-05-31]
CAD/FreeCad/Frame/gonia1.fcstd
40.0 x 40.0 x 40.0 mm

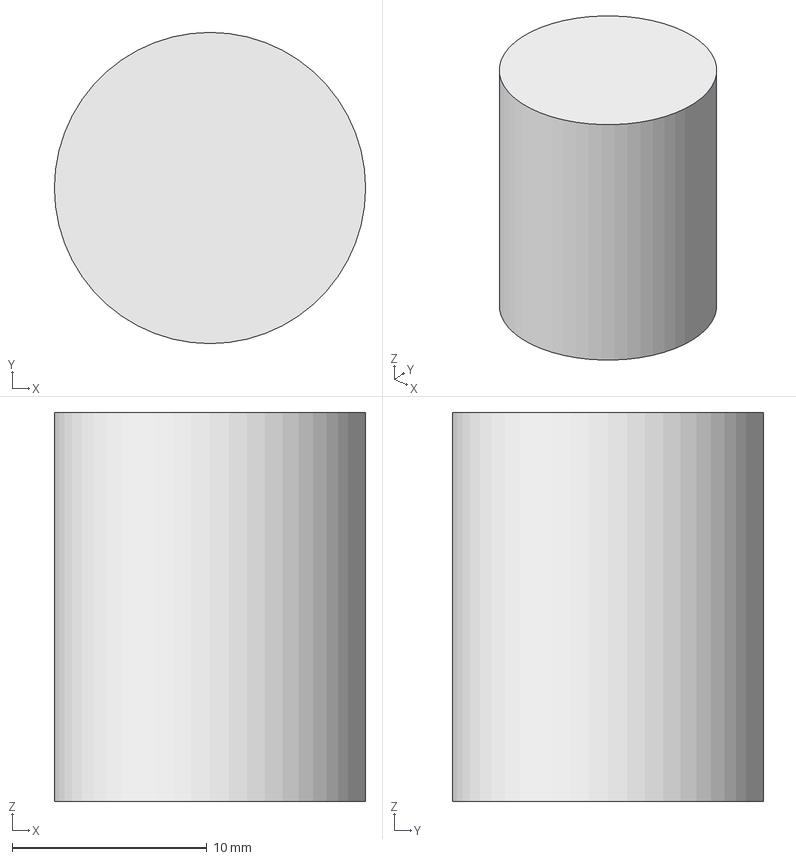
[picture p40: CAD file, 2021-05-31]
CAD/FreeCad/skiasi/sfina1.fcstd
16.0 x 16.0 x 20.0 mm

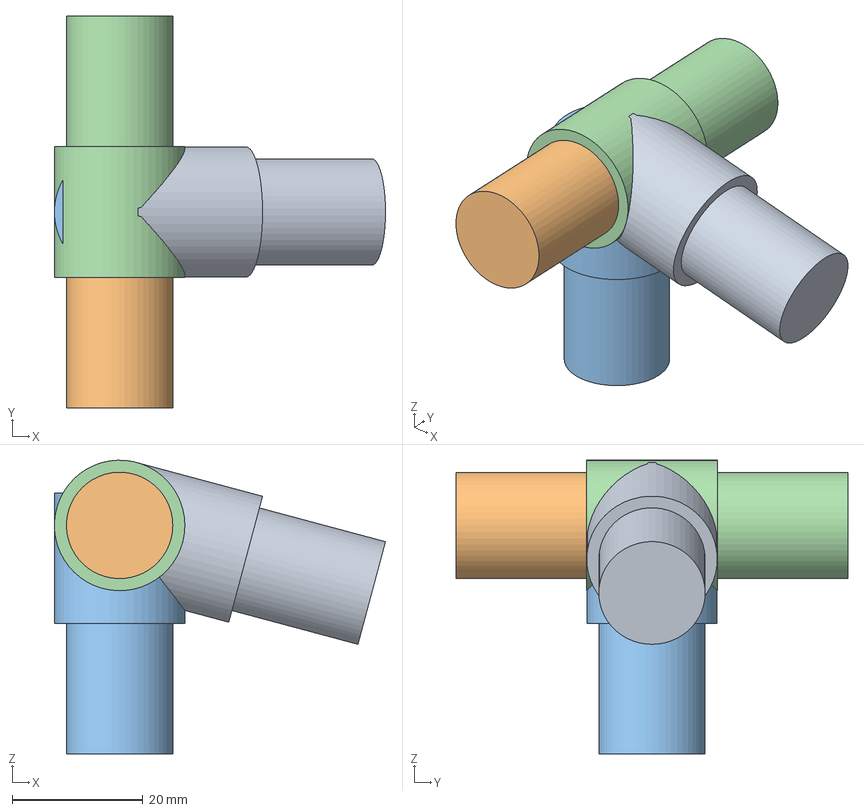
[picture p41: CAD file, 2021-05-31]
CAD/FreeCad/Frame/gonia+75.FCStd
50.7 x 60.0 x 45.0 mm

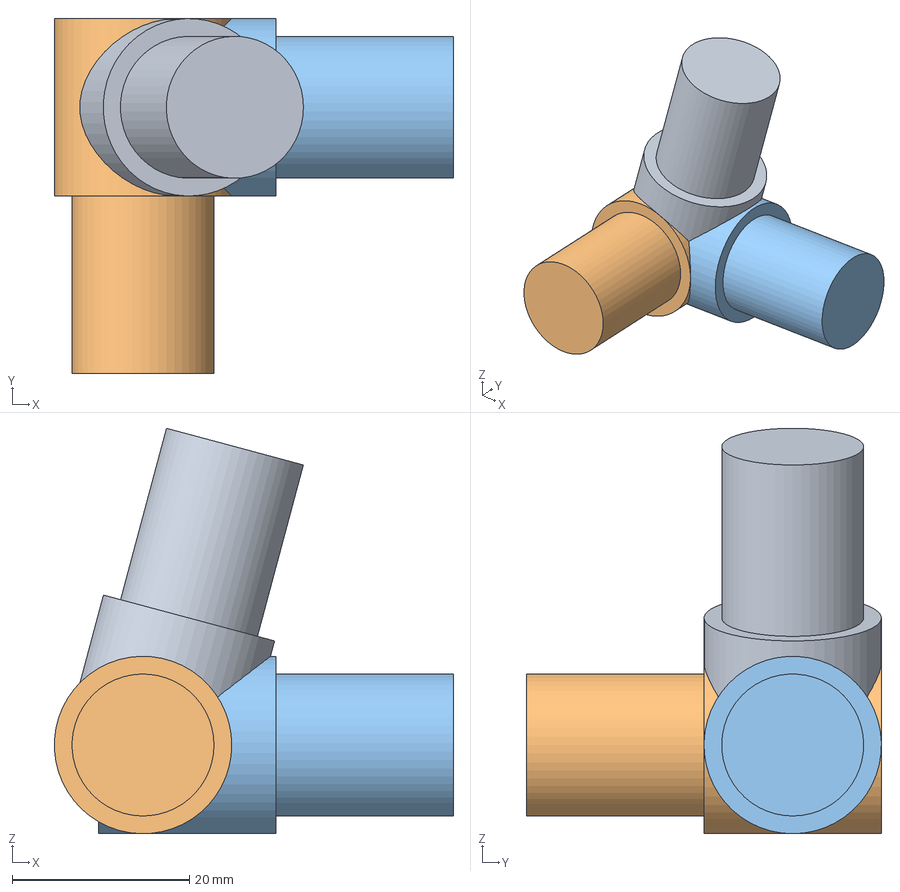
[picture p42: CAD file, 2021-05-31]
CAD/FreeCad/Frame/gonia75_r.fcstd
45.0 x 40.0 x 45.7 mm

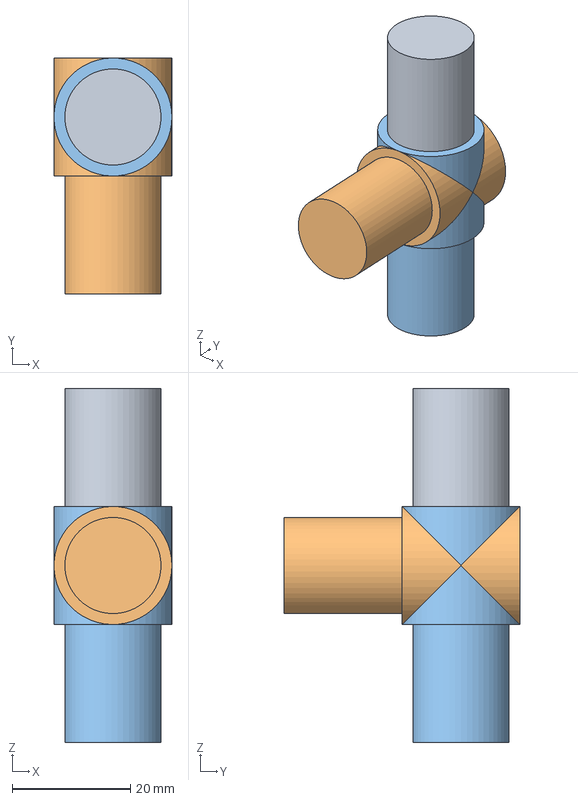
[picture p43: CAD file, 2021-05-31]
CAD/FreeCad/Frame/goniaT.FCStd
20.0 x 40.0 x 60.0 mm

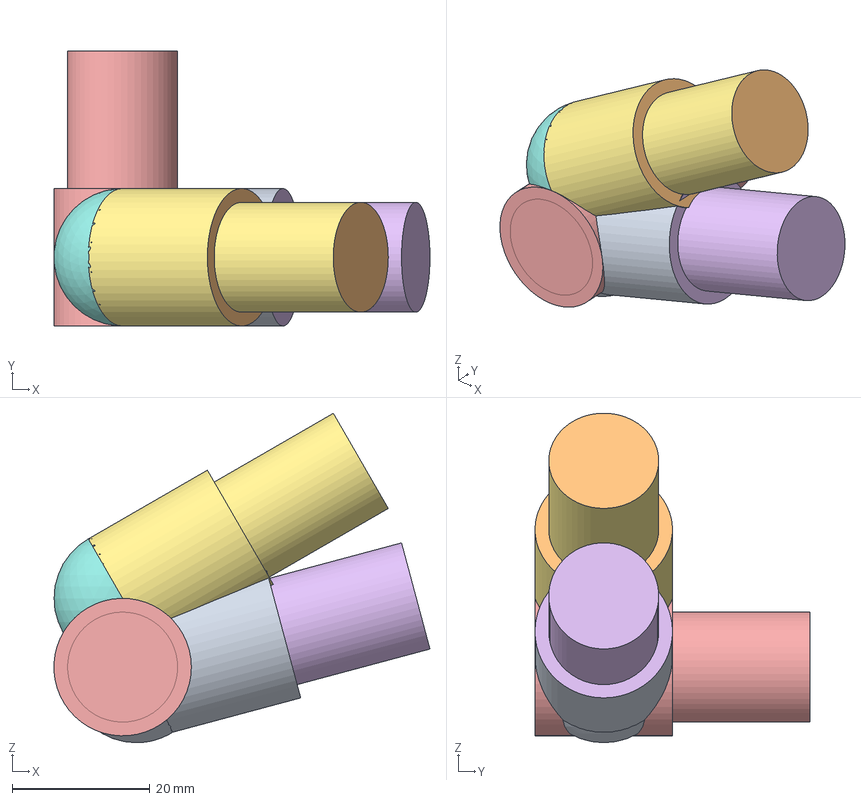
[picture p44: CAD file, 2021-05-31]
CAD/FreeCad/Frame/gonia15_r.fcstd
54.7 x 40.0 x 47.9 mm
Fusion001 (Mirror #1)
Fusion002 (Mirror #2)
Fusion (Mirror #3)
Sphere (Mirror #4)
Sphere001 (Mirror #5)

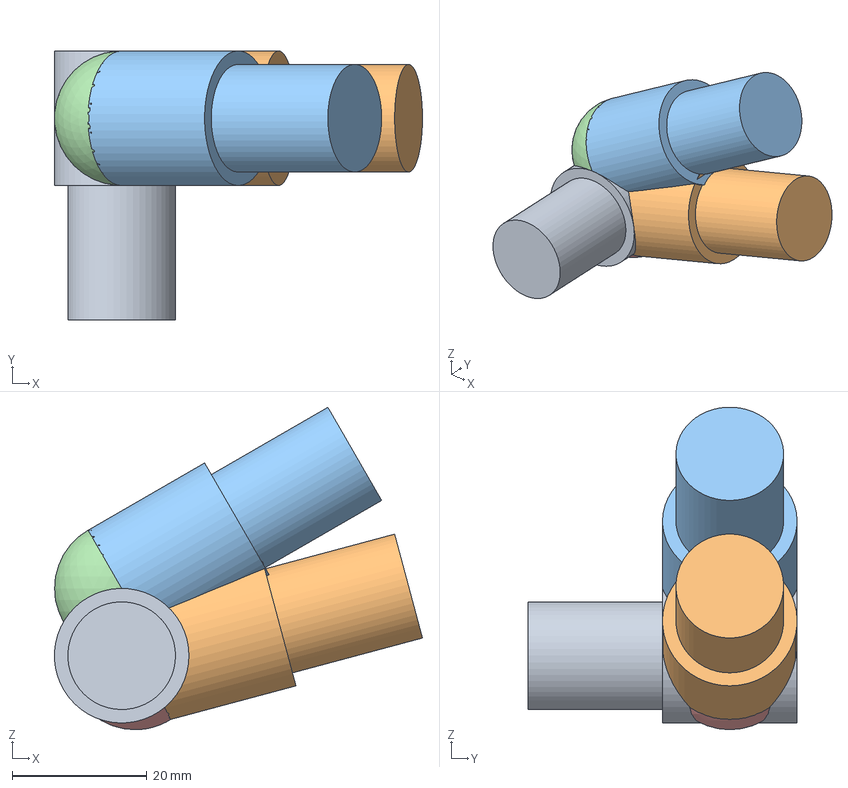
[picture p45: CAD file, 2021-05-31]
CAD/FreeCad/Frame/gonia15_l.fcstd
54.7 x 40.0 x 47.9 mm

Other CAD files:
CAD/STL/skiasi/koyrtina.stl
CAD/FreeCad/Frame/gonia_w_base.FCStd
CAD/FreeCad/Frame/gonia75_l.fcstd
CAD/FreeCad/Frame/gonia2.FCStd
CAD/STL/frame.stl
CAD/STL/skiasi/sfina1.stl

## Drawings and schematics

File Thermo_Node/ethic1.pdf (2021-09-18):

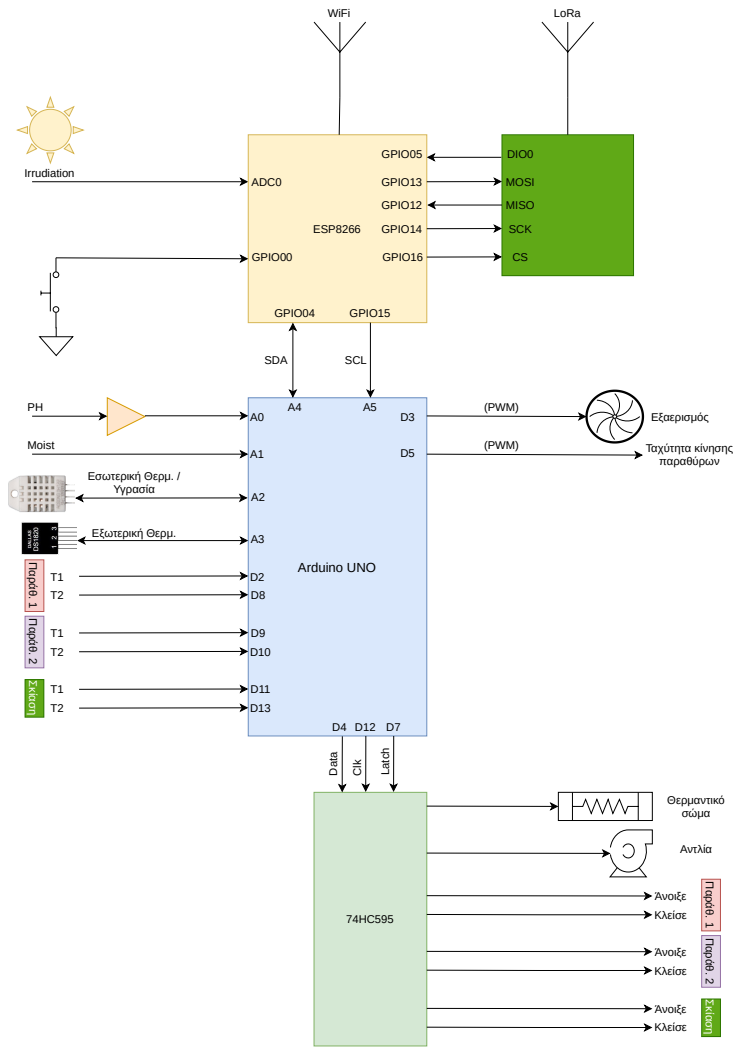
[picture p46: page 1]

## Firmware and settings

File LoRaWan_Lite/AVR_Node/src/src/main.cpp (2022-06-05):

/*** LoRa WAN Lite Node ***/
#include <Arduino.h>
#include <avr/pgmspace.h>
#include <avr/wdt.h>
#include <EEPROM.h>
#include "definitions.h"
#include "thermo.h"
#include "functions.h"
#include "thermo_functions.h"
#include "cmd.h"
#include "commands.h"
#include "encrypt.h"
#include "lora.h"
#include "ClassA_Dev.h"
#include "base64.hpp"

//Μήνυμα έως 128 χαρακτήρες //230
//------------          1         2         3         4         5         6         7         8         9        10        11        12        13        14        15        16        17        18        19        20        21        22        23                                                                                                
//------------ 12345678901234567890123456789012345678901234567890123456789012345678901234567890123456789012345678901234567890123456789012345678901234567890123456789012345678901234567890123456789012345678901234567890123456789012345678901234567890
//char m[] =  "@*Hello world 12345678 preveza prevezas stavros1234 -----1 sdsdd fgfgfg   rrrtt    ~~~~~~``````m mmm ##### $$$$$$$$$$$ ><><>---."; //Χρήση Character Array
//char m[] =  "Test Preveza: ";
String tmp_str;

void setup() 
{
  cmdInit(115200);
  while (!Serial);        //Περίμενε
  pinMode(FAN_PIN, OUTPUT);
  pinMode(SCLK_PIN, OUTPUT);
  pinMode(STCP_PIN, OUTPUT);
  pinMode(P_LOAD, OUTPUT);
  pinMode(SDATA_IN_PIN, INPUT);
  pinMode(STATUS_LED, OUTPUT); 
  pinMode(LED1, OUTPUT);
  blink_times_d(3, 15, 400);  //Αναβόσβησε 3 φορές γρήγορα
  eeprom_init();
  //Εμφάνισε κατάσταση
  Serial.println(F("***** ETHIC [Stavros S. Fotoglou - 1o EPAL PREVEZAS - EK PREVEZAS] *****"));
  lora_init();
  randomSeed(analogRead(A2));
  //Παραγωγή κλειδιών βάσει του κλειδιού 64bit και αποθήκευση στον καθολικό πίνακα keys 16x8
  keys_generator();
  LoRa.idle();   //Πήγαινε το Modem σε κατάσταση Idle
  init_thermo();  //Αρχικοποίηση θερμομέτρων 1-wire
  dht.begin();    //Αρχικοποίηση DHT22
  dout_status = 0;
  writeHC595(0);  //Κάνε Off όλες τις εξόδους αν έχει σκουπίδια μετά το reset
  init_commands(); //Αρχικοποίησε εντολές για την σειριακή γραμμή εντολών
  get_lora(1, 0);  //Εμφάνισε αρχική κατάσταση του LoRa MoDem
  delay(1000);
  win_speed = 210; //160 - 255 Ταχύτητα PWM για κίνηση παραθύρων
  air_stength = 0; //70 - 200 Ταχύτητα PWM για εξαερισμό
  interval1 = interval2 = interval3 = millis();
  imed_flag = true; //Στην αρχή να διαβάσει αισθητήρες χωρίς να περιμένει και να κάνει άμεσα εκπομπή. Το 1ο μήνυμα είναι χωρίς επιβεβαίωση λήψης
  status_str = "";
  uptime = 0;
  rssi = -160;
  //verb = 1; //Βγάλε σχόλιο αν θέλουμε verbosity 1 ή 2
  wdt_enable(WDTO_8S); //Βάλε το Watch Dog στα 8 sec
}

void loop() 
{
 String moist_str, skia_str, w1stat_str, w2stat_str, heat_str, pump_str, uptime_str;
 //--- Βγάλε σχόλιο παρακάτω ώστε να δέχεται εντολές από σειριακή κονσόλα. Επίσης στην γραμμή 68 ClassA_Dev.h ---
 cmdPoll(); //Έλεγξε για εντολή στην κονσόλα
 act(); //Διάβασε διακόπτες και κίνησε ενεργοποιητές
 if (strlen(instr) > 0)
    {
     Serial.print(F(">>>>>"));
     Serial.println(instr);
     cmd_parse(instr); //Ψάξε για εντολή
     instr[0]='\0';
    }
 //Αν έφτασε ο χρόνος δειγματοληψίας ή απαιτεί άμεση εκπομπή τότε διάβασε τιμές αισθητήρων
 if (((millis() - interval1) > AQUIRE_MS) || imed_flag)
    {
     ReadSensors();
     status_str = "";
     //Εξωτερική Θερμ. ; Εσωτερική Θερμ. ; Υγρασία ; Ph ; Ένταση Ηλιακής ακτιν. ; Στάθμη νερού (U/D = Up/Down) ; Κατάσταση κουρτίνας (O/C/S = Open/Close/Step) ;
     //Κατάσταση παραθύρου 1 (O/C/S) ; Κατάσταση παραθύρου 2 (O/C/S) ; Ταχύτητα παραθύρων ; Ταχύτητα εξαερισμού ; Θέρμανση (O/F = On/ofF) ; Αντλία (O/F)
     /*(din_status & _BV(DIN_MOIST)) ? moist_str = "U" : moist_str = "D"; 
     (!(din_status & _BV(DIN_SKT1))) ? skia_str = "O" : ((!(din_status & _BV(DIN_SKT2))) ? skia_str = "C" : skia_str = "S");
     (!(din_status & _BV(DIN_W1T1))) ? w1stat_str = "O" : ((!(din_status & _BV(DIN_W1T2))) ? w1stat_str = "C" : w1stat_str = "S");
     (!(din_status & _BV(DIN_W2T1))) ? w2stat_str = "O" : ((!(din_status & _BV(DIN_W2T2))) ? w2stat_str = "C" : w2stat_str = "S");
     (dout_status & _BV(DOUT_LAMP)) ? heat_str = "O" : heat_str = "F";
     (dout_status & _BV(DOUT_PUMP)) ? pump_str = "O" : pump_str = "F"; */
     uptime_str = String(uptime);
     status_str = t_ext_str + ";" + t_int_str + ";" + hum_str + ";" + ph_str + ";" + irrad_str + ";" + String(din_status) + ";" + String(dout_status) + ";" +
                  String(win_speed) + ";" + String(air_idx) + ";" + String(rssi) + ";" + uptime_str; //";4294967296"
     /*status_str = t_ext_str + ";" + t_int_str + ";" + hum_str + ";" + ph_str + ";" + irrad_str + ";" + moist_str + ";" + skia_str + ";" + 
                  w1stat_str + ";" + w2stat_str + ";" + String(win_speed) + ";" + String(air_idx) + ";" + heat_str + ";" + pump_str + ";" + 
                  String(rssi) + ";" + uptime_str; //";4294967296"*/
     if (verb == 2)
         Serial.println(status_str); //Debug
     interval1 = millis();
    }

 //Αν πέρασε ο χρόνος ή απαιτεί άμεση εκπομπή τότε κάνε προετοιμασία για εκπομπή πακέτου
 if (((millis() - interval2) > LORA_PREP_MS) || imed_flag)
    {
     //tmp_str = m;
     tmp_str = status_str;
     payload_len = encrypt((byte*)tmp_str.c_str(), (byte*)out); //Κρυπτογράφησε με DES
     //raw(m, out); //ή ετοίμασε μη κρυπτογραφημένα δεδομένα
     //Serial.println(out); //Debug
     //Serial.println(yy); //Debug   
     //decrypt((byte*)out, oo, yy); //Debug για δοκιμή αλγορίθμου
     interval2 = millis();
    }
 
 //Αν πέρασε ο χρόνος ή απαιτεί άμεση εκπομπή τότε κάνε εκπομπή πακέτου
 if (((millis() - interval3) > LORA_TX_MS) || imed_flag)
    {
     time_4_tx = true;
     //Αν απαιτηθεί άμεση εκπομπή μετά από αλλαγή κάποιου ενεργοποιητή τότε να μη ζητήσει επιβεβαίωση λήψης
     if (imed_flag)
        {
         confRqst = UNCONFIRM; //CONFIRM_REQ ή UNCONFIRM;
         imed_flag = false;
        }
     else
         confRqst = CONFIRM_REQ; //Αν εκπέμπει περιοδικά την κατάσταση όταν έρθει ο χρόνος, να ζητάει επιβεβαίωση λήψης από το δίκτυο
     interval3 = interval2 = interval1 = millis();
     uptime += UPTIME_SEC;
    }

 //Αν είναι ενεργοποιημένο κάνε εκπομπή του πακέτου και περίμενε για λήψη. Εκτελείται συνέχεια
 if (time_4_tx)
    {
     //Κάνε εκπομπή και άνοιξε τα παράθυρα λήψης
     ClassA_Dev();
     //Αν έχει ληφθεί κάποιο frame στα παράθυρα λήψης, τότε συνέχισε με έλεγχο και επεξεργασία
     if (rx_state == RX_DONE)
         handleRxFrame();
    }
 //Αλλιώς αν τελείωσε ο προηγούμενος κύκλος εκπομπής - λήψης
 else
    {
     //Αν έχει λάβει έγκυρο option και θέλει να ανοίξει αμέσως ένα νέο κύκλο Tx
     if (optOK)
        {
         optOK = false; //Μην ξαναμπείς εδώ μέχρι να λάβει νέα εντολή MAC
         imed_flag = true; //Στείλε τώρα
        }
     //Αν είναι ενεργοποιημένο τότε άλλαξε συχνότητα ή DR   
     if (updateLater == 2)
        {
         updateLoRa();
         updateLater = 0;
        }
    }
 
 wdt_reset(); //Σε περίπτωση που κολλήσει να κάνει reset
}

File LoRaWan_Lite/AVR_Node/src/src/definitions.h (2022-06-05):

#define VERSION                "1.0 beta"

//======================= Ορισμοί θυρών του Arduino =========================================
#define STATUS_LED             9
#define LED1                  13
#define SDATA_IN_PIN          19  //A5-Διαβάζει σειριακά δεδομένα από το HC597
#define SCLK_PIN               7  //Το pin SHCP του HC597 και για το HC595
#define STCP_PIN               4  //Το pin STCP ή Parallel Load του HC597
#define SDATA_OUT_PIN          4  //Το pin Data Serial για το HC595 είναι ίδιο με πάνω
#define P_LOAD                 8  //Το pin STCP ή Parallel Load του HC595
#define FAN_PIN                5  //Το PWM pin για ανεμιστήρες
#define PH_PIN                A0  //Αναλογική είσοδος για μέτρηση Ph
#define IRRAD_PIN             A1  //Αναλογική είσοδος για ένταση ηλιακής ακτινοβολίας
#define WINDOW_SPEED_PIN       6  //Το PWM pin για ταχύτητα παραθύρων

//====================== Ορισμοί εισόδων του Port Expander ===================================
#define DIN_W1T1               0  //Τερματικός T1 για παράθυρο 1 - Ανοιχτό ή 'A' στην κλέμα
#define DIN_W1T2               1  //Τερματικός T2 για παράθυρο 1 - Κλειστό ή 'B' στην κλέμα
#define DIN_W2T1               2  //Τερματικός T1 για παράθυρο 2 - Ανοιχτό ή 'A' στην κλέμα
#define DIN_W2T2               3  //Τερματικός T2 για παράθυρο 2 - Κλειστό ή 'B' στην κλέμα
#define DIN_SKT1               4  //Τερματικός T1 για κουρτίνα σκίασης - Μαζεμένη
#define DIN_SKT2               5  //Τερματικός T2 για κουρτίνα σκίασης - Απλωμένη
#define DIN_MOIST              6  //Στάθμη νερού πλήρης
//---------------------------- 7  //To 7 είναι διαθέσιμο για ψηφιακή είσοδο

//====================== Ορισμοί εξόδων του Port Expander ====================================
#define DOUT_LAMP              0  //Θερμαντικό σώμα
#define DOUT_PUMP              1  //Αντλία ποτίσματος
#define DOUT_W1_C1             2  //Παράθυρο 1 επαφή 1
#define DOUT_W1_C2             3  //Παράθυρο 1 επαφή 2
#define DOUT_W2_C1             4  //Παράθυρο 2 επαφή 1
#define DOUT_W2_C2             5  //Παράθυρο 2 επαφή 2
#define DOUT_SK_C1             6  //Κουρτίνα σκίασης επαφή 1
#define DOUT_SK_C2             7  //Κουρτίνα σκίασης επαφή 2

//Ορισμός του Clk Pulse για shift registers
#define clockPulse()  {digitalWrite(SCLK_PIN, HIGH);digitalWrite(SCLK_PIN, LOW);}


#define MSG_LEN               80 //Μέγιστο μήκος μηνύματος
#define NODE_ADDRESS          0xAB31 //Διεύθυνση του κόμβου
#define NO_ACK                0x00
#define UNCONFIRM             0x00  //Unconfirmed
#define CONFIRM_REQ           0x80  //Confirmed

//Ορισμοί χρονιστών λειτουργίας του συστήματος
//#define AQUIRE_MS             25000   //Κάθε 25 δευτερόλεπτα (σε msec) διαβάζει αισθητήρες
//Κύκλος εκπομπής μηνυμάτων από 10sec έως 1hour - καλό είναι κάθε 1 λεπτό
#define TX_CYCLE              ((1 * 60000) - 2000) //Κύκλος χρήσης LORA κάθε 1 λεπτό (εκπομπή 0,1% ή 0,6 για SF9)
#define AQUIRE_MS             TX_CYCLE //π.χ. στα 58 sec διάβασε κατάσταση αισθητήρων
#define LORA_PREP_MS          (TX_CYCLE + 1000)  //Κάθε n λεπτά και 1 sec (σε msec) προετοίμασε πακέτο για εκπομπή
#define LORA_TX_MS            (TX_CYCLE + 2000)  //Κάθε n λεπτά και 2 sec (σε msec) Στείλε το πακέτο
#define UPTIME_SEC            (LORA_TX_MS / 1000)

//Χρόνοι LoRaWan Lite 
#define RX1_TIME              1000000 //1sec (σε μsec) το 1ο παράθυρο λήψης
#define RX2_TIME              2000000 //2sec (σε μsec) το 2ο παράθυρο λήψης
#define RX1_OPEN_TOLLER       50 //μsec ο χρόνος που κάνει να εκτελεστεί η receive_single()
#define TX_RETRIES            3   //Είναι το NbTrans δηλ. επανάληψη πακέτου αν δεν το λάβει ο server

//Συχνότητες λειτουργίας
#define FREQ_START            433050000
#define FREQ_END              434790000   //Εύρος 1.74MHz δηλαδή 28 κανάλια 62.5KHz
#define FREQUENCY             433150000   //Προκαθορισμένη συχνότητα λειτουργίας
/* Αρχικό κανάλι βάζω το 433.150 και μετά αυξάνω ανά 200Khz δηλ. 433.350, 433.550, 433.750, 433.950, 434.150, 434.350, 434.550, 434.750
δηλαδή έχω 9 κανάλια
*/

#define EEPROM_START          0  //Αρχική διεύθυνση της EEPROM
#define FREQUENCY_ADDR        EEPROM_START                  //Αποθηκεύεται η συχνότητα
#define SF_ADDR               FREQUENCY_ADDR + sizeof(long) //Αποθηκεύεται το sf
#define BW_ADDR               SF_ADDR + sizeof(byte)        //Αποθηκεύεται το bw
#define CR_ADDR               BW_ADDR + sizeof(long)        //Αποθηκεύεται το cr 4/5, 4/6, 4/7, 4/8
#define POWER_ADDR            CR_ADDR + sizeof(byte)        //Αποθηκεύεται η ισχύς 2-20 dBm
#define END1_ADDR             POWER_ADDR + sizeof(byte)     //Τέλος
#define END2_ADDR             END1_ADDR + sizeof(byte)

//------- Blink Codes ----------------
#define COM_STATE_OK          0
#define SETUP_ERROR           1
#define NO_REPLY_ERROR        2
#define TX_ENABLE             3

//Ορισμός κλειδιού κωδικοποίησης του μηνύματος
const byte enc_key[] = {0x21, 0x02, 0xf8, 0xaf, 0x88, 0x00, 0x09, 0x6e}; //Κλειδί 64bit
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

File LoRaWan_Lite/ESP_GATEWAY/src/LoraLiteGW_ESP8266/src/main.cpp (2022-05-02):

//pio run --target uploadfs
#include <Arduino.h>
#include <ESPAsyncTCP.h>
#include "LittleFS.h"
#include <SPI.h>
#include <LoRa.h>
#include "definitions.h"
#include "base64.hpp"
#include "functions.h"
#include "lora.h"
#include "network.h"

//Ορισμός Timer
static os_timer_t intervalTimer;

byte txbuf[256];      //Η buffer με το μήνυμα LoRa προς εκπομπή
byte tmp_buff[512];
String tmp1, data;
int frame_len = 0;
byte ptr1, ptr2;

void setup() 
{
 pinMode(BUILTIN_LED, OUTPUT);
 digitalWrite(BUILTIN_LED, HIGH);
 Serial.begin(115200);
 Serial.println();
 Serial.println(F("========== LoRa Lite Gateway (c)2022 by Stavros S. Fototglou [SV6GMP] =========="));
 //Προετοιμασία συστήματος αρχείων 3 Mbyte
 if (!LittleFS.begin()) 
    {
     Serial.println("LittleFS initialization failed!");
     while (1) yield(); // Stay here twiddling thumbs waiting
    }
 Serial.println(F("\r\nLittleFS available!"));
 LittleFS.begin();
 //Αν ξεκίνησε το σύστημα αρχείων στην εσωτερική Flash 4Mbyte
 //Εμφάνισε ελεύθερο χώρο από το σύστημα SPIFFS
 FSInfo fs_info;
 LittleFS.info(fs_info);
 float fileTotalKB = (float)fs_info.totalBytes / 1024.0; 
 float fileUsedKB = (float)fs_info.usedBytes / 1024.0; 
 char tmp[40];
 sprintf(tmp, "Used %.1fKb of total %.1fKb", fileUsedKB, fileTotalKB);
 Serial.println(tmp);
 readSettings_net(); //Διάβασε ρυθμίσεις δικτύου από αρχείο
 readSettings_LORA(); //Διάβασε ρυθμίσεις LoRa από αρχείο
 //Ρουτίνα εξυπηρέτησης αν γίνει σύνδεση TCP με τον server π.χ. www.google.com 
 test_client->onConnect(&onConnect, test_client); //Στο network.h
 led_pat = 0b0111111111; //Αρχική κατάσταση
 initNetwork(); //Αρχικοποίηση δικτύου WiFi, IP, NTP και WebServer
 blink_per = millis();
 initLoRa(); //Αρχικοποίηση πομποδέκτη LoRa
 pull_timer = millis(); 
 txbuf[0] = '\0'; //Αρχικά άδειο buffer εκπομπής
 tx_wait = true; //Αρχικά περιμένει να πάρει χρόνο tmst από τον NW Server
 //tx_tmst = 4294967295; //Αρχικά το timestamp είναι μεγάλο ώστε να μην κάνει εκπομπή σε TX window έως να πάρει τιμή από τον NW Server
 //packets[0].tx_tmst=2345;
 ptr1 = ptr2 = 0;
 //Κάθε 30 sec κάνε έλεγχο σύνδεσης
 os_timer_disarm(&intervalTimer); //Απενεργοποίηση Timer
 os_timer_setfn(&intervalTimer, &testcon, NULL); //Ορισμός ρουτίνας εξυπηρέτησης χωρίς ορίσματα στο network.h
 os_timer_arm(&intervalTimer, 30000, true);  //Ενεργοποίηση με επανάληψη κλήσης κάθε 30 sec
 uptime = 0;
}

void loop() 
{
 if (InternAvail == "true")
     timeClient.update(); //Όταν φτάσει η στιγμή ανανέωσε την ώρα από τον NTP Server
 //Αν πέρασε ~1sec μετά την λήψη δηλ. το παράθυρο RX1 ή RX2 (2sec) τότε στείλε τα δεδομένα στο Node
 if ((micros() >= (packets[ptr2].tx_tmst - PRE_OPEN_TIME)) && (tx_state == TX) && (ptr1 != ptr2)) //996400
     {
      Serial.print("------");
      Serial.println(packets[ptr2].tx_tmst);
      LoRa.setSpreadingFactor(packets[ptr2].sf); //Βάλε το SF στη τιμή που ζήτησε ο NW Server
      LoRa.setSignalBandwidth(packets[ptr2].bw); //Βάλε το BW στη τιμή που ζήτησε ο NW Server
      //* Κατάσταση εκπομπής *
      if (packets[ptr2].frame_len > 0)
         {
          if (packets[ptr2].ipol == "true") //Αν το θέλει ο NW Server
              LoRa.enableInvertIQ(); //Για εκπομή από πύλη προς Node θα αντιστρέψει τα I/Q ώστε να μην ακούει η μια πύλη την άλλη
          LoRa.beginPacket(); //Ετοίμασε πακέτο LoRa προς αποστολή στο Node
          LoRa.write(packets[ptr2].txbuf, frame_len); 
          LoRa.endPacket();                     // Κλείσε το πακέτο και στείλτο
          //Φτιάχνει ένα string με πληροφορίες για το πακέτο που έλαβε ώστε να εμφανιστεί στο web dashboard
          unsigned short frameId = packets[ptr2].txbuf[4] * 256 + packets[ptr2].txbuf[3]; 
          sprintf(tx_pkt_log, "%s | %02X%02X | %04X | %03d <br>\n",curTime().c_str(), packets[ptr2].txbuf[2], packets[ptr2].txbuf[1], frameId, packets[ptr2].frame_len);
          txpkt_cnt++;
          //Μετακίνησε τις γραμμές κατά μια θέση σβήνοντας την παλαιότερη γραμμή
          for (byte i = 0; i < LOG_LINES-1; i++)
               tx_pkts_log[i] = tx_pkts_log[i+1];
          //Βάλε στην τελευταία γραμμή τα νεότερα δεδομένα
          tx_pkts_log[LOG_LINES-1] = String(tx_pkt_log);
          //Φτιάξε το τελικό string το οποίο θα στέλνει στο web interface
          tx_pkts_str = "";
          for (byte i = 0; i < LOG_LINES; i++)
               tx_pkts_str += tx_pkts_log[i];     
         }
      LoRa.disableInvertIQ(); //Στο τέλος της εκπομπής τα I/Q γυρίζουν κανονικά
      LoRa.setSpreadingFactor(lora_sf.toInt()); //Γύρισε πάλι στο προκαθορισμένο SF
      LoRa.setSignalBandwidth(lora_bw.toInt()); //Γύρισε πάλι στο προκαθορισμένο BW
      LoRa.receive(); //Επιστροφή σε κατάσταση λήψης
      tx_state = RX;
      Serial.println(F("* Transmit to Node ->"));
      ptr2++;
      if (ptr2 >= BUFF_LEN)
          ptr2 = 0;
     }
 
 //Κάθε 30sec στείλε πακέτο PULL στον NW Server
 if (millis() - pull_timer > PULLDATA_INTERVAL)
    {
     pull_data();
     pull_timer = millis();
     NWSrv_State = "false"; //Αφού στείλει Pull, θεώρησε ότι είναι offline και αν πάρει απάντηση θα γίνει true
     uptime += 30; //Ενημέρωσε το uptime κατά 30 sec
     tim += 30; //Ενημέρωσε το epoch time κατά 30 sec αν δεν λειτουργεί το NTP
     if (WiFi.status() == WL_CONNECTED)
         S_Strength = String(WiFi.RSSI()) + "dBm";
     else
         S_Strength = "";
    }
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

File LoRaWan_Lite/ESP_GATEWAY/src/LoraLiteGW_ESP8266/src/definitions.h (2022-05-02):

#define VERSION       "1.01"

//#define LED1                  2 //Build in Led  
#define BUILTIN_LED           2
#define PULLDATA_INTERVAL     30000  //Κάθε 30sec στέλνει pull data στον server
#define PRE_OPEN_TIME         2000

byte head[12];  //Η επικεφαλίδα του πακέτου UDP
char isotime[25]; //Ο χρόνος λήψης σε μορφή ISO
unsigned long pull_timer; //Ο χρονιστής για Pull Data
byte last_h1, last_h2;
unsigned long blink_per; //Ο χρονιστής για το LED
String ipol;
unsigned long tx_tmst;
byte sf, size;
unsigned int bw;
bool tx_wait;

#define BUFF_LEN     5   //Πόσα πακέτα από τον NW Server αποθηκεύει μέχρι να μεταδοθούν από το LoRa
struct pkt{ byte txbuf[256]; //Μέγιστο μήκος κάθε πακέτου 256 bytes
            int frame_len;
            byte sf;
            long bw;
            unsigned long tx_tmst;
            String ipol;
          };

pkt packets[BUFF_LEN];

//--------------------- Όνομα του Server για να κάνει έλεγχο σύνδεσης ------------------------------------
const char *testhost = "www.google.com";  //Η διεύθυνση για να κάνει έλεγχο σύνδεσης στο διαδίκτυο
const char *update_host = "hostname";
String Dl_Path = "/path/";
String Dl_Filename; //Η πλήρης διαδρομή του αρχείου π.χ. /hostname/path/test.txt δημιουργείται μέσα στην download() στο network.h
String FileName, Version; //Το όνομα του αρχείου στο SPIFFS
byte Dl_State = 0;
bool CanUpdate;

unsigned long tim; //Χρονιστής epoch αν δεν έχει σύνδεση διαδικτύου

//-------------------------- Μεταβλητές σύνδεσης μέσω WiFi -----------------------------------------------
String SetAP, AP_SSID, AP_CHANNEL, AP_ENCRYPT, AP_KEY, SetSTA, ST_SSID, ST_KEY, IP_STATIC, IP_ADDR, IP_MASK,
       IP_GATE, IP_DNS, NTP_TZ, BROW_TO, NTP_SRV, NET_SRV, NET_SRV_PORT, MQTT_USER, MQTT_PASS, MQTT_CLIENT, LOG_NAME="admin", LOG_PASS="preveza";
String InternAvail = "false", NWSrv_State = "false", DLFileName = "", Dl_OK = "false", S_Strength = "";

bool conn = false; //Γίνεται true όταν υπάρχει σύνδεση Internet

#define LOG_LINES   10
char rx_pkt_log[60], tx_pkt_log[60];
String rx_pkts_log[LOG_LINES], rx_pkts_str, tx_pkts_log[LOG_LINES], tx_pkts_str;
unsigned int rxpkt_cnt = 0, txpkt_cnt = 0;

//---------------------------------------------------------------------
unsigned long uptime; //Χρονιστής uptime για έλεγχο συνεχόμενης λειτουργίας

//----------------------------- Μεταβλητές LORA -----------------------------------------
#define FREQ_START            433050000
#define FREQ_END              434790000   //Εύρος 1.74MHz δηλαδή 28 κανάλια 62.5KHz
#define FREQUENCY             433150000
#define SF                            9
#define BW                       125000     //Hz
#define CR                            5
#define SYNCWORD                    194     //0xC2 ή 0x34 για LORAWAN
#define POWER                        17     //dBm
String lora_freq, lora_sf, lora_cr, lora_bw, lora_sync, lora_power; 

char t_ext_str[6], t_int_str[6];
short cur_Irrad, cur_Irrad_avg = 0, max_Irrad = -50;
char cur_Irrad_str[6];
float t_ext, t_int, max_t_ext = -40.0, max_t_int = -40.0, min_t_ext = 100.0, min_t_int = 100.0;
float dht_temp = 0.0;
char dht_temp_str[6];
float humidity = 0.0, humWet = 0.0, max_humidity = -10.0, min_humidity = 200.0;
char hum_str[6]; //Εδώ αποθηκεύει την τιμή της υγρασίας
char wet_str[6];
char max_t_ext_timestamp[35], min_t_ext_timestamp[35], max_t_int_timestamp[35], min_t_int_timestamp[35], max_Irrad_timestamp[42], max_Humidity_timestamp[35], min_Humidity_timestamp[35];
float T_int_S = 0, T_ext_S = 0, dht_temp_S = 0, humidity_S = 0; //Αθροίσματα τιμών κάθε 1sec
float T_int_SHr = 0, T_ext_SHr = 0, humidity_SHr = 0, dht_temp_SHr = 0; //Αθροίσματα τιμών κάθε 5min
//-----------------------------------------------------------------------------

unsigned short led_pat = 0;
